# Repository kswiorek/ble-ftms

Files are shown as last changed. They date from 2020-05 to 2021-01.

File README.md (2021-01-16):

# Arduino BLE Indoor Bike Fitness Machine

This project uses two ESP32 boards to emulate an expensive indoor bike trainer and a power meter.<br/>
<br/>
One ESP measures power and cadence on a crank, the other receives these values, emulates a trainer and forwards the data. It also receives the simulation parameter from a computer and sets position of the resistance screw accordingly.<br/>
The data is also displayed on a 12864 screen and the user is able to change the resistance in ERG mode and the gears in simulation mode.<br/>
The user can also load a file with resistance values and times when to set them on an SD card.<br/>
The whole "realistic physics" part turned out to be more annoying to set up than realistic, so I added a configurator, with which the user can graphicaly define the function converting from the simulated grade to the resistance. More described in the instructable.
<br/><br/>
The promissed instructable <a href="https://www.instructables.com/DIY-Indoor-Bike-Smart-Trainer/?cb=1604870523">https://www.instructables.com/DIY-Indoor-Bike-Smart-Trainer/?cb=1604870523</a>

If you want to dig deaper into the code I highly suggest reading the "Fitness Machine Service" specifications
<a href="https://www.bluetooth.com/specifications/gatt/">https://www.bluetooth.com/specifications/gatt/</a>

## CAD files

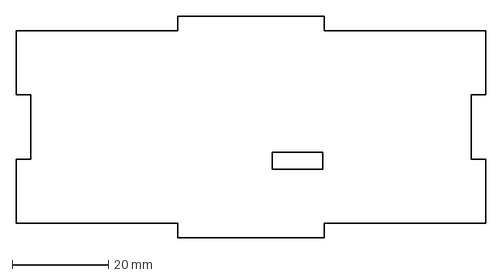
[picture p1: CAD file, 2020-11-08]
dxf/console/right.dxf
97.3 x 46.0 mm

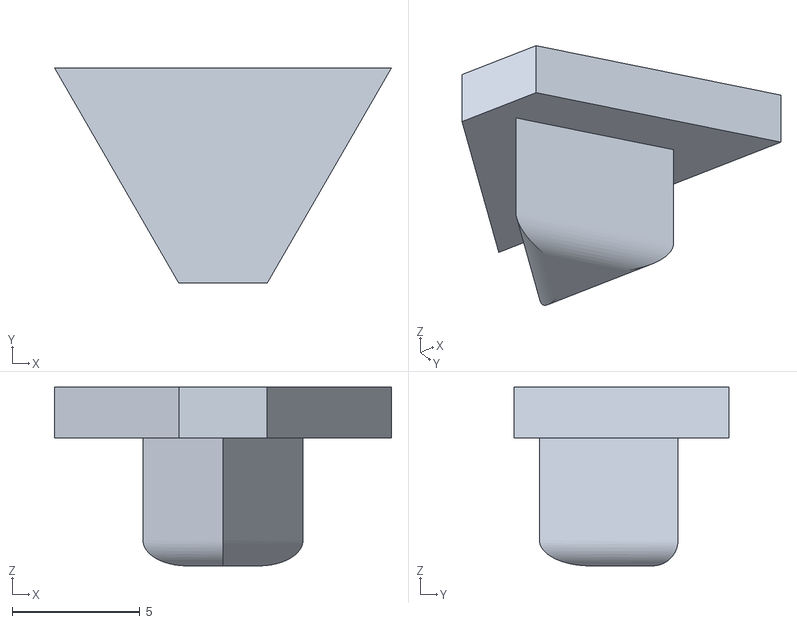
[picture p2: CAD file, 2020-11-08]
stl/bt1.stl
13.2 x 8.43 x 7.00

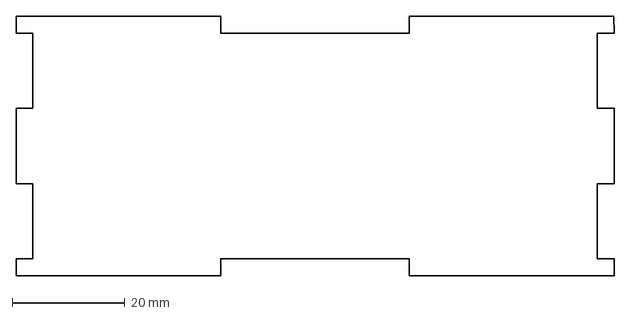
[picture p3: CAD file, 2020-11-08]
dxf/console/back.dxf
106.0 x 46.0 mm

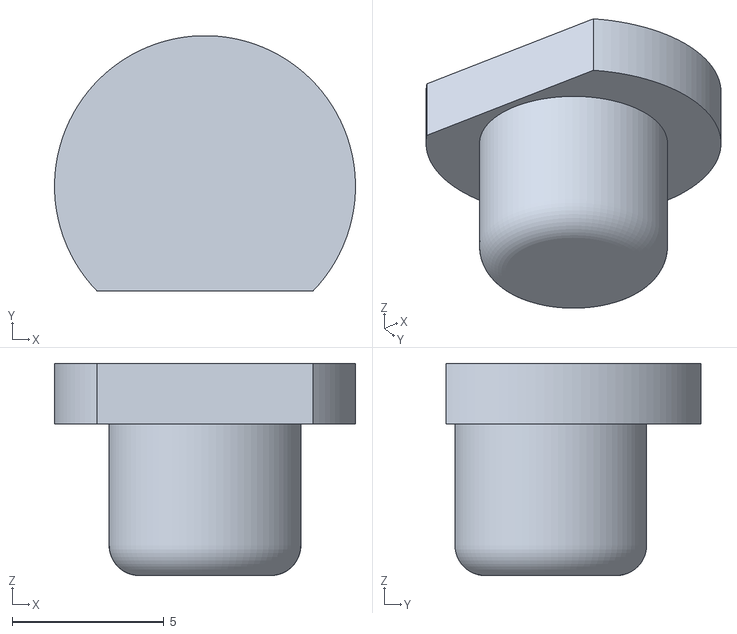
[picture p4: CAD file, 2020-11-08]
stl/bt3.stl
9.93 x 8.43 x 7.00

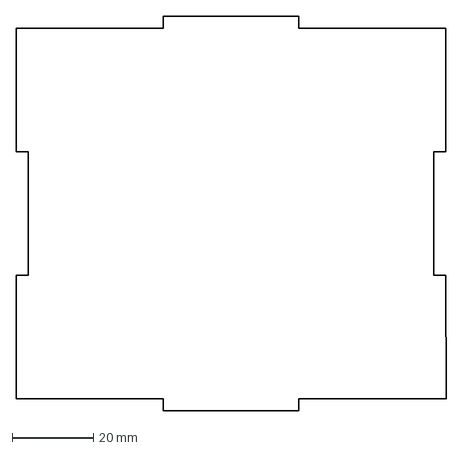
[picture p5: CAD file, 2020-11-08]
dxf/console/bottom.dxf
106.0 x 97.3 mm

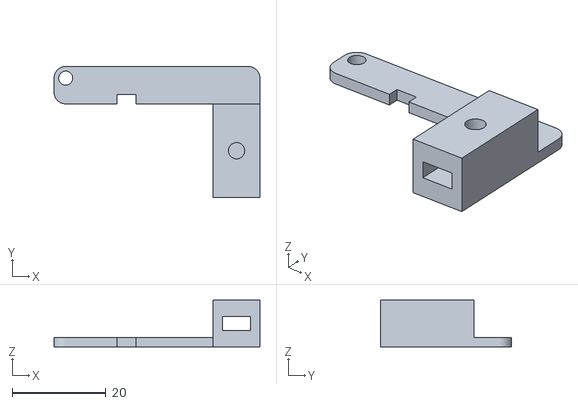
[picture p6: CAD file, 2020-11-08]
stl/pcb holder.stl
44.0 x 28.0 x 10.0

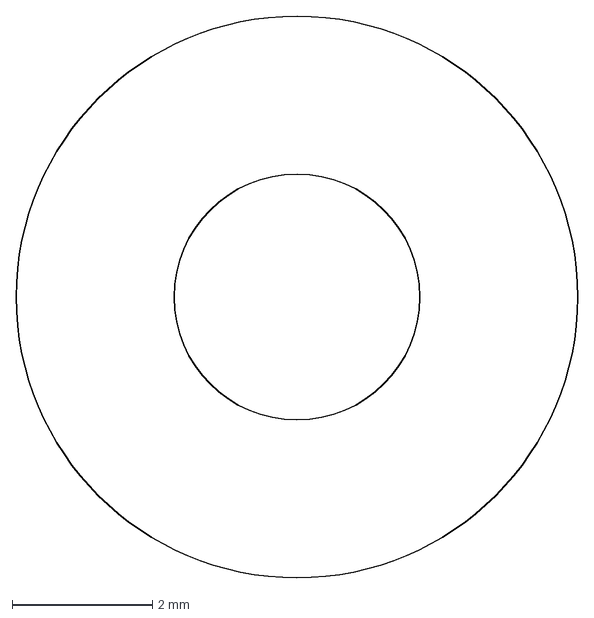
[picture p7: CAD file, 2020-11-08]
dxf/console/spacer.dxf
8.00 x 8.00 mm

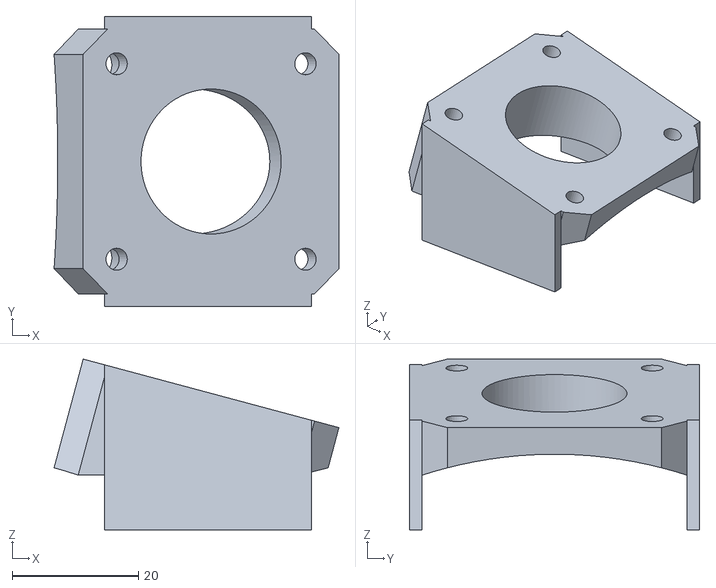
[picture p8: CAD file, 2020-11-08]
stl/motor mount.stl
45.2 x 46.0 x 27.1

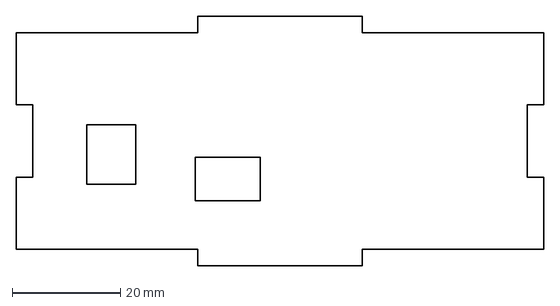
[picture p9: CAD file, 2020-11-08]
dxf/console/left.dxf
97.3 x 46.0 mm

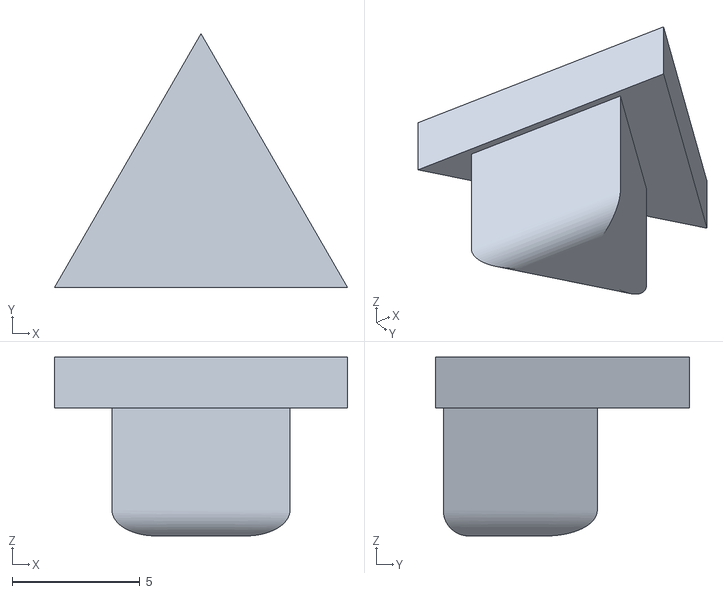
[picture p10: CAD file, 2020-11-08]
stl/bt2.stl
11.5 x 9.93 x 7.00

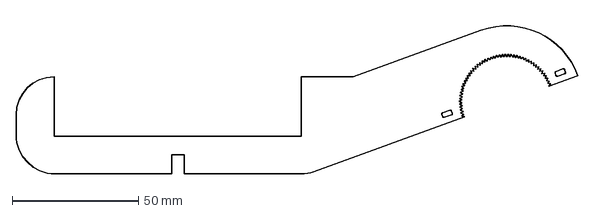
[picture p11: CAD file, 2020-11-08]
dxf/console/arm.dxf
222.8 x 62.6 mm

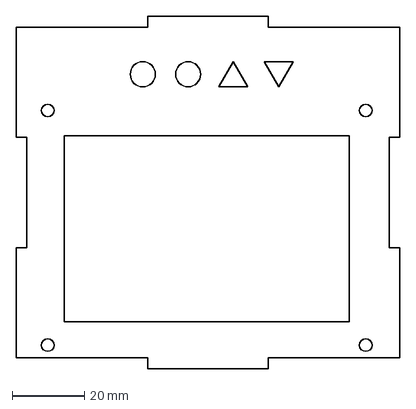
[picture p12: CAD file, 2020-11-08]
dxf/console/top.dxf
106.0 x 97.3 mm

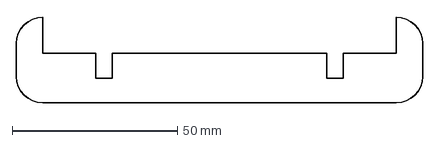
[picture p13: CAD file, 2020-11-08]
dxf/console/connector.dxf
123.0 x 26.0 mm

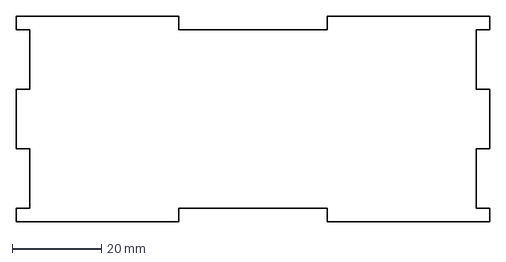
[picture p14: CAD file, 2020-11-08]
dxf/console/front.dxf
106.0 x 46.0 mm

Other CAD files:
fusion360/console.f3d
fusion360/motor mount.f3d
fusion360/pcb holder.f3d
fusion360/spacer.f3d

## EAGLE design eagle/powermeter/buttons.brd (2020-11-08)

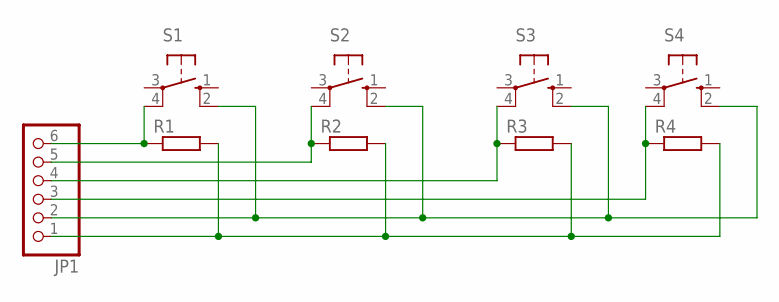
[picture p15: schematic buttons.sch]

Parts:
JP1: PINHD-1X6/90; 1X06/90
R1, R2, R3, R4: R-EU_0207/10; 0207/10
S1, S2, S3, S4: 10-XX; B3F-10XX

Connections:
unnamed: JP1.6, R1.1, S1.4 (P1)
unnamed: JP1.5, R2.1, S2.4 (P1)
unnamed: JP1.4, R3.1, S3.4 (P1)
unnamed: JP1.3, R4.1, S4.4 (P1)
unnamed: JP1.2, S1.2 (S1), S2.2 (S1), S3.2 (S1), S4.2 (S1)
unnamed: JP1.1, R1.2, R2.2, R3.2, R4.2

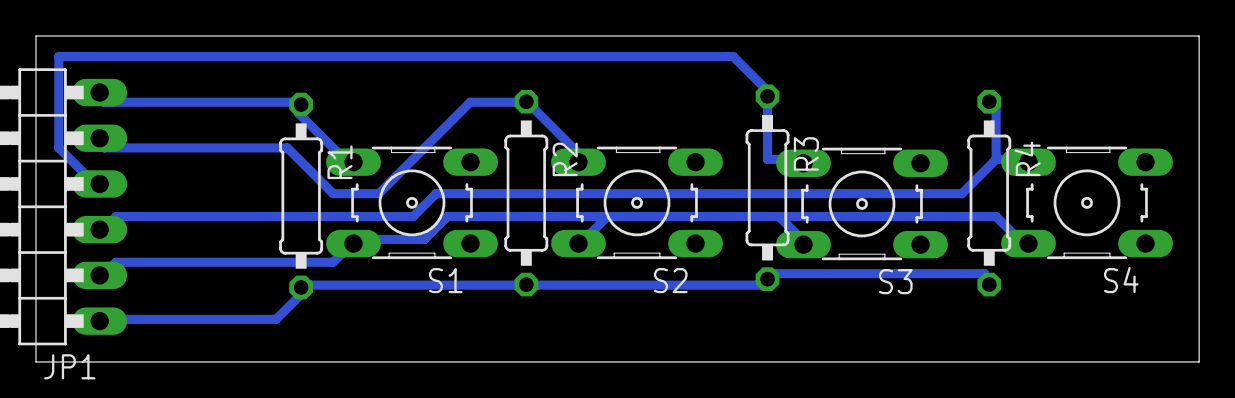
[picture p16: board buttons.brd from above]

Board: 2 copper layers, 64.6 x 18.1 mm, 9 parts (0 on the bottom side), 6 nets.

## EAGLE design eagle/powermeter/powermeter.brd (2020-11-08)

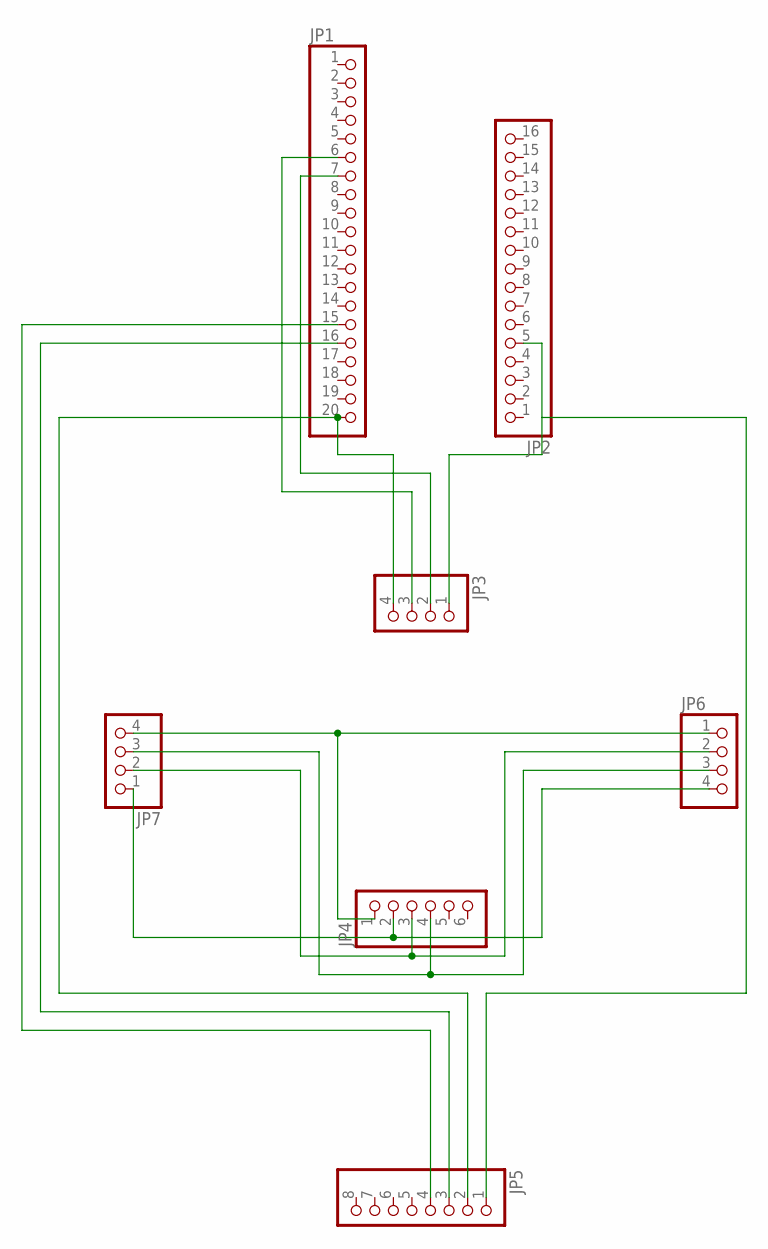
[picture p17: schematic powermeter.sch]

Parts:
JP1: PINHD-1X20; 1X20
JP2: PINHD-1X16; 1X16
JP3, JP6, JP7: PINHD-1X4; 1X04
JP4: PINHD-1X6; 1X06
JP5: PINHD-1X8; 1X08

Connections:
unnamed: JP4.1, JP6.1, JP7.4
unnamed: JP4.2, JP6.4, JP7.1
unnamed: JP4.3, JP6.2, JP7.2
unnamed: JP4.4, JP6.3, JP7.3
unnamed: JP1.20, JP3.4, JP5.2
unnamed: JP1.6, JP3.3
unnamed: JP1.7, JP3.2
unnamed: JP1.15, JP5.4
unnamed: JP2.5, JP3.1, JP5.1
unnamed: JP1.16, JP5.3

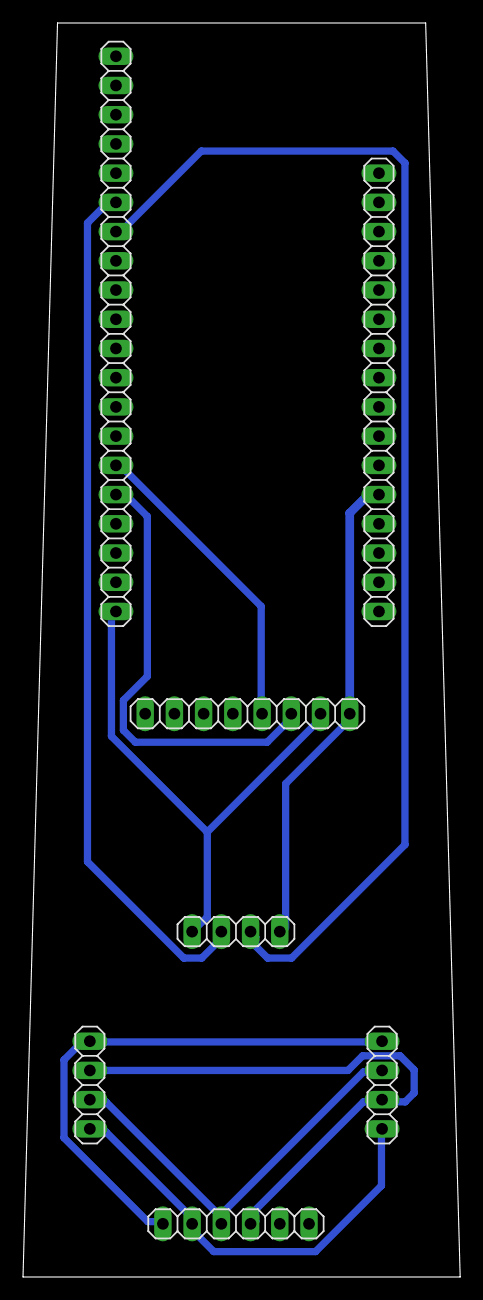
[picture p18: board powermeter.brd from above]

Board: 2 copper layers, 38.0 x 109.0 mm, 7 parts (0 on the bottom side), 10 nets.

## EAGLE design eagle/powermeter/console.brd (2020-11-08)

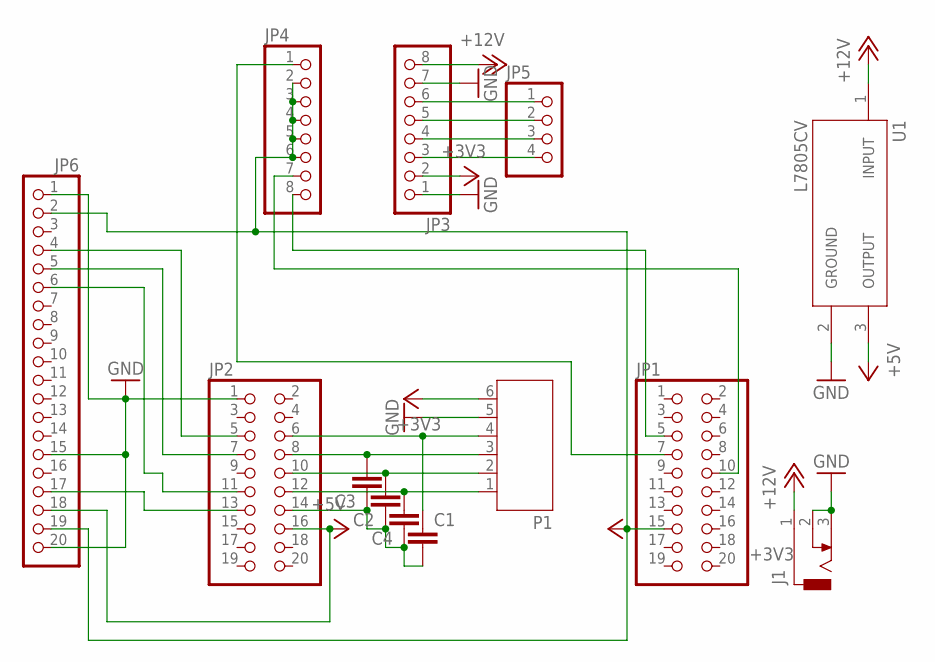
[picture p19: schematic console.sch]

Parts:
C1, C2, C3, C4: C-EU025-030X050; C025-030X050
J1: DCJ0303
JP1, JP2: PINHD-2X10; 2X10
JP3, JP4: PINHD-1X8; 1X08
JP5: PINHD-1X4/90; 1X04/90
JP6: PINHD-1X20; 1X20
P1: JST-PH6
U1: L7805CV; TO255P1040X460X1968-3

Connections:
+3V3: JP1.15, JP3.2, JP4.2, JP4.3, JP4.4, JP4.5, JP4.6, JP6.2, JP6.19, P1.6
+5V: JP2.16, JP6.18, U1.3 (OUTPUT)
+12V: J1.1, JP3.8, U1.1 (INPUT)
GND: J1.2, J1.3, JP2.1, JP3.1, JP3.7, JP6.1, JP6.15, JP6.20, P1.5, U1.2 (GROUND)
unnamed: C2.2, JP2.10, P1.2
unnamed: C3.2, JP2.8, P1.3
unnamed: C1.1, JP2.6, P1.4
unnamed: JP2.5, JP6.4
unnamed: JP2.13, JP6.17
unnamed: JP2.7, JP6.5
unnamed: C4.2, JP2.12, P1.1
unnamed: JP1.7, JP4.1
unnamed: JP3.6, JP5.1
unnamed: JP1.10, JP4.7
unnamed: JP1.5, JP4.8
unnamed: JP3.5, JP5.2
unnamed: JP3.4, JP5.3
unnamed: JP3.3, JP5.4
unnamed: C1.2, C2.1, C3.1, C4.1, JP2.14
unnamed: JP2.11, JP6.6

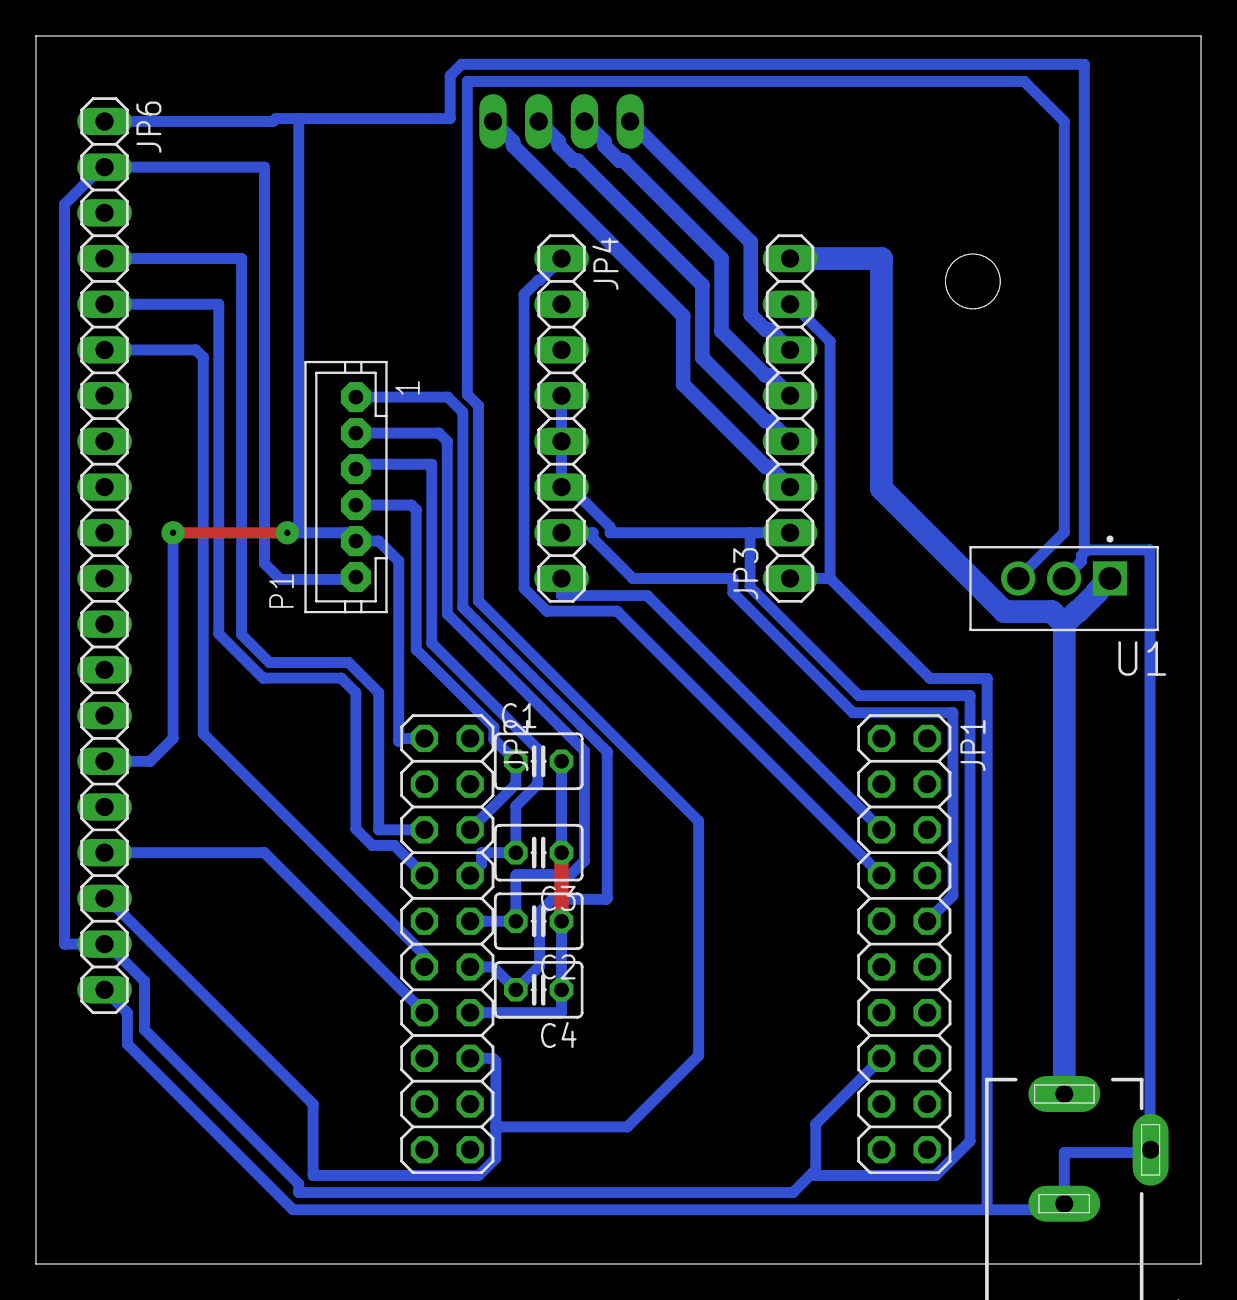
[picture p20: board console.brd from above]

Board: 2 copper layers, 64.8 x 68.2 mm, 13 parts (1 on the bottom side), 20 nets.

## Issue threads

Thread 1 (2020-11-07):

Instructables

paytufo, 2020-11-07:
Did you do the instructables guide finaly?

kswiorek, 2020-11-07:
I unfortunately didn't have the time, but I think you've motivated me enough to finally do this. I never actually suspected anyone would look at this.

paytufo, 2020-11-08:
Thank you! I'm starting to learn some code but I'm pretty noob. I've many time searching this solution to my dumb bike trainer.  My idea is to build an open bike trainer for people who like DIY. A BLDC trainer like Tacx NEO or Wahoo. Your code could be the first step to develop this trainer.

kswiorek, 2020-11-08:
I've made the instructable, I still need to upload some other files here, but the main thing is done [https://www.instructables.com/DIY-Indoor-Bike-Smart-Trainer/?cb=1604870523](url)

doudar, 2020-11-09:
Oh wow....I've skimmed across your repo before but now that you did the instructable. Now I know what its for. lol.........check this out:

https://github.com/doudar/SmartSpin2k-PlatformIO

I bet we could have saved each other a bunch of time. I've been wracking my head on that buggy ESP bluetooth library for a year in my spare time.

Maybe we should collaborate? :)

kswiorek, 2020-11-09:
Nice project! Far more professional than mine... It looks like you've got everything figured out. I will gladly help, but I'm not much of a coder - this whole thing is bodged together from some examples. I focused more on the physics of a realistic simulation. In theory this should be just as a normal bike - it even has the correct ratios of gears taken from a real road bike.
I also prefer to mount everything on one PCB - the wires often break and short, it always annoys me.

doudar, 2020-11-09:
I would *love* to see a carrier PCB if you thought it was possible. Possibly with an integrated dc-dc converter. I don't really have issues with wires breaking if they're done correctly but they do make assembly a pain.

Anyway, awesome project of yours too! I wouldn't have had any idea on where to start with that load cell stuff that you did.

Closed 2020-11-08.

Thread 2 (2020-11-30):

Thany you!

sife14, 2020-11-30:
I just want to say thank you for your amazing work. I have searched for implementation of the FTMS for ESP32 for hours until I found your amazing project. I really like the idea of the virtual gearing.

The only problem I experienced with your implementation, was an unstable connection to the virtual bike trainer software, which I fixed by adding a delay in the main loop. It seems like it was sending data to fast. I don't know if this issue also existed in the original code, since I modified your code quite a bit to fit to my hardware needs.

kswiorek, 2020-11-30:
I'm glad that I could help. I wanted to share this so I can save people some time, as I spent tens of hours without the help of any examples.
The delay might have helped - the graphical LCD I'm using takes quite a long time to write to, so the delay creates itself, but without it the loop may indeed run too quickly. I don't like using the "delay" function, because it stops any inputs and the refreshing of the LCD. I would use the something like this: `if millis()%100 { [send data] }` this would send the data every 100ms, but the LCD would still refresh as quickly as it can.

doudar, 2020-11-30:
I didn't look at the code, but vtaskdelay() should be your go to on the ESP32 as it lets other threads run. Regular delay() blocks anything else from running.

Closed 2020-12-04.

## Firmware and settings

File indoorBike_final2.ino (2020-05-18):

#include "BLE.h"
#include <SPI.h>
#include <U8g2lib.h>
#include <AccelStepper.h>
#include <EEPROM.h>
#include "soc/timer_group_struct.h"	
#include "soc/timer_group_reg.h"	// nesessary for avoiding watchdog triggering on the stepper core
#include "FS.h"
#include "SD.h"
#include "SPI.h"

#define wholeWeight 720			// weight of bicycle and rider
#define wheelDiameter 0.33
#define motorRpm 60				// RPM of the stepper motor

#define motorSteps 3200.0		// steps per revolution, needs to be float for calculations

const int levelSteps = 40;		// resistance steps 
#define rotations 4.5			// rotations of the screw for the steps

#define button1 25				// pin of pause button 
#define button2 32				// pin of enter button
#define button3 22				// pin of decrement button
#define button4 21				// pin of increment button

#define interruptTime 70		// miliseconds for debouncing buttons

const int lowCal[3] =	{ 60, 10, 30 }; // cadence[rpm], level, power[W]
const int highCal[3] =	{ 60, 20, 150 }; // cadence[rpm], level, power[W]

float lowTorque = lowCal[2] / ((lowCal[0] / 60.0) * 6.28);		// wheel torque on the low point of calibration
float highTorque = highCal[2] / ((highCal[0] / 60.0) * 6.28);	// wheel torque on the high point of calibration

int gearIndex;
#define gearNum 22			// number of gears
float gears[gearNum] = { 	// gear ratios
	0.323529412,
	0.382352941,
	0.441176471,
	0.458333333,
	0.5		   ,
	0.541666667,
	0.558823529,
	0.617647059,
	0.625	   ,
	0.705882353,		 
	0.708333333,
	0.791666667,
	0.823529412,
	0.875	   ,
	0.941176471,
	1		   ,
	1.088235294,
	1.166666667,
	1.235294118,
	1.333333333,
	1.541666667,
	1.75
};

// lcd defined
U8G2_ST7920_128X64_F_SW_SPI u8g2(U8G2_R0, /* clock=*/ 16 /* A4 */, /* data=*/ 17 /* A2 */, /* CS=*/ 0 /* A3 */, /* reset=*/ 4);
AccelStepper stepper = AccelStepper(1, 33, 26); // stepper defined

TaskHandle_t Task1;	// label for the stepper task

int16_t setPos, curPos;
int scroll;
float level;
bool zero;
bool psB;
bool enterB;
bool menu;

void IRAM_ATTR incr()	  // function to increment the level, gear index or scroll, with debouncing
{
	static unsigned long last_interrupt_time = 0;
	unsigned long interrupt_time = millis();
	if (interrupt_time - last_interrupt_time > interruptTime)
	{
		if (!menu) 
		{
			if (!sim)
			{
				level = int(level);
				level++;
			}
			else
			{
				gearIndex++;
				gearIndex = constrain(gearIndex, 0, gearNum-1);
			}
		}
		else scroll++;
	}
	last_interrupt_time = interrupt_time;
}
void IRAM_ATTR decr()	  // function to decrement the level, gear index or scroll, with debouncing
{
	static unsigned long last_interrupt_time = 0;
	unsigned long interrupt_time = millis();
	if (interrupt_time - last_interrupt_time > interruptTime)
	{
		if (!menu) 
		{
			if (!sim)
			{
				level = int(level);
				level--;
			}
			else
			{
				gearIndex--;
				gearIndex = constrain(gearIndex, 0, gearNum-1);
			}
		}
		else scroll--;
	}
	last_interrupt_time = interrupt_time;
}

void IRAM_ATTR enter()
{
	static unsigned long last_interrupt_time = 0;
	unsigned long interrupt_time = millis();
	if (interrupt_time - last_interrupt_time > interruptTime)
	{
		if (menu) enterB = true;
		menu = true;
		psB = true;
	}
	last_interrupt_time = interrupt_time;
}

void IRAM_ATTR ps()
{
	static unsigned long last_interrupt_time = 0;
	unsigned long interrupt_time = millis();
	if (interrupt_time - last_interrupt_time > interruptTime)
	{
		if (!menu) psB = !psB;
		menu = false;
	}
	last_interrupt_time = interrupt_time;
}

void setup() {
	Serial.begin(115200);
	BLEDevice::init("IndoorBike"); // name of the ble devicev
	while (!connectToServer());
	InitBLEServer();
	
	u8g2.begin();
	u8g2.clearBuffer();
	while (!SD.begin()) {    	   // while the card isnt initialized display message
		u8g2.setFont(u8g2_font_ncenB14_tr);
		u8g2.setCursor(33, 30);
		u8g2.print("WLOZ");
		u8g2.setCursor(28, 48);
		u8g2.print("KARTE");
		u8g2.sendBuffer(); 
		delay(200);   
	}

	xTaskCreatePinnedToCore(	   // setup the task for the second core
	                  Task1code,
		/* Task function. */
	                  "Task1",
		/* name of task. */
	                  10000,
		/* Stack size of task */
	                  NULL,
		/* parameter of the task */
	                  1,
		/* priority of the task */
	                  &Task1,
		/* Task handle to keep track of created task */
	                  0);          /* pin task to core 0 */
	
	stepper.setMaxSpeed(motorRpm / 60 * 3200);	// setup the motor																						 
	stepper.setSpeed(motorRpm / 60 * 3200);
	stepper.setAcceleration(12800);
	stepper.setEnablePin(27);					// enable pin
	stepper.setPinsInverted(0, 0, 1);

	pinMode(button1, INPUT);
	pinMode(button2, INPUT);
	pinMode(button3, INPUT);
	pinMode(button4, INPUT);	   	

	EEPROM.begin(4);
  
	level = EERead(2);
	Serial.println(level);
	curPos = EERead(0);
	Serial.println(curPos);
	stepper.setCurrentPosition(curPos);
	stepper.enableOutputs();
	menu = false;
	psB = true;
}
File file;
int values[64], valIndex;
long pauseStart, pauseEnd, pauseTot, playTime;
bool pauseTest, levelTest = true;
int zeroCnt, loopCnt;
void loop() {
	if (sim) // if in simulation mode (not ERG)
	{	
		float setTorque = (((grade / 10000.0)*wholeWeight) * wheelDiameter)+5.5;  // calculated set resistance torque on the wheel + torque on flat road
		Serial.println(setTorque);
		Serial.println(grade);
		float pedalTorque = gears[gearIndex]*setTorque;	 // set torque on the crank
		Serial.println(gears[gearIndex]);
		Serial.println(pedalTorque);
		level = mapF(pedalTorque, lowTorque, highTorque, lowCal[1], highCal[1]);	// mapped to the level settings
		Serial.println(level);
		level = constrain(level, 0, levelSteps);
		
																	
	}
	speedOut = (cadenceIn * 2.75 * 2.08 * 60*gears[gearIndex]) / 10;						// calculated speed, required by the specification
	indoorBikeDataCharacteristicData[2] = (uint8_t)(speedOut & 0xff);
	indoorBikeDataCharacteristicData[3] = (uint8_t)(speedOut >> 8);							// speed value with little endian order
	indoorBikeDataCharacteristicData[4] = (uint8_t)((cadenceIn * 2) & 0xff);				
	indoorBikeDataCharacteristicData[5] = (uint8_t)((cadenceIn * 2) >> 8);					// cadence value
	indoorBikeDataCharacteristicData[6] = (uint8_t)(constrain(powerIn, 0, 4000) & 0xff);
	indoorBikeDataCharacteristicData[7] = (uint8_t)(constrain(powerIn, 0, 4000) >> 8);		// power value, constrained to avoid negative values, although the specification allows for a sint16
    
	indoorBikeDataCharacteristic.setValue(indoorBikeDataCharacteristicData, 8);				// values sent
	indoorBikeDataCharacteristic.notify();	 												// device notified
	
	if (digitalRead(button2))zeroCnt++; // counter for button hold used for homing
	else zeroCnt = 0;
	if (!menu) { // if menu isn't on, display values
		u8g2.clearBuffer();
		u8g2.setFont(u8g2_font_ncenB14_tr);
		u8g2.setCursor(100, 32 + 7);
		if (!sim) u8g2.print(int(level));
		else	 u8g2.print(gearIndex);
		u8g2.setCursor(2, 30);
		u8g2.print(String(powerIn));
		u8g2.setCursor(2, 50);
		u8g2.print(String(cadenceIn));
		u8g2.setFont(u8g2_font_6x10_tf);
		u8g2.setCursor(1 + (12*String(powerIn).length()), 30);
		u8g2.print("W");
		u8g2.setCursor(1 + (12*String(cadenceIn).length()), 50);
		u8g2.print("rpm");
		u8g2.setFont(u8g2_font_6x13_tf);
		u8g2.setCursor(2, 11);			
		u8g2.print(file.name());
		if (psB && millis() % 2000 > 1000) // blinking "pause" sign
		{
			u8g2.setCursor(97, 11);
			u8g2.print("PAUZA");
		}
		u8g2.sendBuffer();
	}
	else
	{
		u8g2.clearBuffer();
		u8g2.drawRFrame(0, 0, 128, 64, 7);
		File root = SD.open("/");
		file = root.openNextFile();
		if (!file) {
			u8g2.setFont(u8g2_font_ncenB14_tr);
			u8g2.setCursor(30, 32 + 7);
			u8g2.print("Brak plikow");	 // no files
		}
		else  // display file list end show cursor
		{
			String files[32];
			int i = 0;
			u8g2.setFont(u8g2_font_6x13_tf);
			while (file) {        
				if (!(bool)file.isDirectory())
				{
					files[i] = file.name();
					i++;
				}
				file = root.openNextFile();
			}
			for (i = 0; i < 5; i++)
			{
				int scrollPrev;
				if (files[int(i + 5*(floor(scroll / 5)))] != "")
				{
					u8g2.setCursor(20, 14 + (i * 11));
					u8g2.print(files[int(i + 5*(floor(scroll / 5)))]);
				}      
			}
			if (files[scroll] == "") scroll = scroll - 1;
			u8g2.setCursor(5, 14 + ((scroll % 5) * 11));
			u8g2.print("->");

			if (enterB)  // chose file and close the menu
			{
				file = SD.open(files[scroll]);
				Serial.println(file.name());
				enterB = false;
				menu = false;
				String content = file.readString();	   //read file contents
				Serial.println(content);

				int lastIndex = 0;
				int index = content.indexOf(";", lastIndex);
				i = 0;
				while (index >= 0) // get the list of settings
				{
					values[i] = content.substring(lastIndex, index).toInt();
					lastIndex = index + 1;
					index = content.indexOf(";", lastIndex);
					i++;
				}
				psB = true;
				pauseTot = pauseTot + playTime;
				valIndex = 0;
			}
		}
		u8g2.sendBuffer();
	}

	if (psB&&pauseTest)			// deal with pausing
	{
		pauseStart = millis();
		pauseTest = false;
	}
	else if (!psB && !pauseTest)
	{
		pauseEnd = millis();
		pauseTest = true;
		pauseTot = pauseTot + (pauseEnd - pauseStart);
	}

	if (!psB)
	{
		playTime = millis() - pauseTot;
		Serial.println(playTime);
		if (values[valIndex] == playTime / 1000 && levelTest)
		{
			levelTest = false;
			level = values[valIndex + 1];
			valIndex = valIndex + 2;
		}
		else if (values[valIndex] != playTime / 1000) levelTest = true;
	}
  
	if (level > levelSteps) level = levelSteps;
	if (level < 0) level = 0;
	if (scroll < 0) scroll = 0;
	setPos = mapF(level, 0.0, levelSteps, 0.0, motorSteps*rotations);
	Serial.print("setPos	");
	Serial.println(setPos);
	if ((curPos != setPos && !zero) && level >= 0 && level <= levelSteps) // move the motor to a new position
	{
    
		stepper.moveTo(setPos);
		curPos = setPos;

		EEWrite(curPos, 0);
		EEWrite(level, 2);
    
		Serial.println(curPos);
		Serial.println(level);
	}
	if (zeroCnt > 30) zero = true;
	Serial.println(zeroCnt);
	if (zero)		 // move to the end of travel until motor loses steps
	{
		Serial.println("Homing");
		curPos = 0;   
		EEWrite(curPos, 0);
		u8g2.clearBuffer();
		u8g2.setFont(u8g2_font_ncenB14_tr);
		u8g2.setCursor(3, 32 + 7);
		u8g2.print("ZEROWANIE");
		u8g2.sendBuffer();
		stepper.setMaxSpeed(300 / 60 * 3200);
		stepper.moveTo(-(int(rotations*motorSteps)));
		//Serial.println(-(rotations*motorSteps));
		delay(5000);
		curPos = 0;  
		level = 0; 
		stepper.setCurrentPosition(0); 
		stepper.setMaxSpeed(motorRpm / 60 * 3200);
		zero = false;
		menu = false;
	}
	//stepper.run();
}

void EEWrite(int16_t inp, int reg) //write a word to eeprom on register
{
	word ee;
	//Serial.println(inp);
	ee = inp & 0xFF00;
	ee = ee >> 8;
	EEPROM.write(reg, ee);
	ee = inp & 0xFF;
	EEPROM.write(reg + 1, ee);
	EEPROM.commit();
}

int16_t EERead(int reg)			   // read a word on register
{
	word ee;
	ee = EEPROM.read(reg);
	ee = ee << 8;
	ee = ee + EEPROM.read(reg + 1);
	return ee;
}
bool test;
void Task1code(void * parameter) {	   // handle the stepper and button on the other core. Interrupts break bluetooth
	for (;;) {
		TIMERG0.wdt_wprotect = TIMG_WDT_WKEY_VALUE;	   // the loop needs to run fast, this disables the watchdog
		TIMERG0.wdt_feed = 1;
		TIMERG0.wdt_wprotect = 0;

		if (stepper.isRunning()) stepper.enableOutputs();
		else                    stepper.disableOutputs();
    
		stepper.run();
		if (digitalRead(button4)) incr();
		if (digitalRead(button3)) decr();
		if (digitalRead(button2)) enter();
		if (digitalRead(button1)) ps();
		delayMicroseconds(10);
	}
}

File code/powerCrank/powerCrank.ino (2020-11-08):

#include "HX711.h"
#include <Adafruit_MPU6050.h>

#include <Wire.h>
#include <math.h>
#include <EEPROM.h>

// all must be floats for calculations
#define sensMin -200941.0  // reading of the sensor with 0 force
#define sensMax -351117.0  // reading of the sensor with weightMax of force
#define weightMax 120.0
#define radius 0.175		   // distance form crank center to pedal center
#define sensRadius 0.115   // distance of the MPU sensor to crank center 

#define zeroAngle 180	   // angle, where to tare - all angles according to the Cycling Power Measurement specifications
						   // left crank forward - 0 degrees
#define freq 0.5		   // notify frequency

#define LOADCELL_DOUT_PIN 16
#define LOADCELL_SCK_PIN 17

Adafruit_MPU6050 mpu;
HX711 scale;

#include <BLEDevice.h>
#include <BLEUtils.h>
#include <BLEServer.h>
#include <BLE2902.h>

#define SERVICE_UUID        "4fafc201-1fb5-459e-8fcc-c5c9c331914b"			// UUID of the service, random, must match the one on the console
#define POWER_CHARACTERISTIC_UUID "beb5483e-36e1-4688-b7f5-ea07361b26a8"	// UUID of the characteristic, random, must match the one on the console
#define CADENCE_CHARACTERISTIC_UUID "ceb5483e-36e1-4688-b7f5-ea07361b26a8"	// UUID of the characteristic, random, must match the one on the console

BLECharacteristic sendPower(POWER_CHARACTERISTIC_UUID, BLECharacteristic::PROPERTY_NOTIFY);
BLECharacteristic sendCadence(CADENCE_CHARACTERISTIC_UUID, BLECharacteristic::PROPERTY_NOTIFY);

// average variables:
// avr - rolling average lasts one rotation or 2 seconds
// avgFin - the final average of avr with the frequency of "freq"
long reading;
float weight, weightOld, power, rpm, avr;
double angle;
float reg[160];	// samples for the rolling average
bool test;

bool tareTest = true;
int samples, cnt, tareCnt, offCnt;
int8_t tare;
long avgFin;

bool _BLEClientConnected = false;

class MyServerCallbacks : public BLEServerCallbacks {
  void onConnect(BLEServer* pServer) {
    _BLEClientConnected = true;
    Serial.println("conn");
  };

  void onDisconnect(BLEServer* pServer) {
    _BLEClientConnected = false;
    Serial.println("disc");
  }
};

void InitBLE() {
    BLEDevice::init("crank");
    BLEServer *pServer = BLEDevice::createServer();
    pServer->setCallbacks(new MyServerCallbacks());
    
	BLEService *pPower = pServer->createService(SERVICE_UUID);

	pPower->addCharacteristic(&sendPower);
	BLE2902* powerDesc = new BLE2902();
	powerDesc->setIndications(1);                                       
	sendPower.addDescriptor(powerDesc);
	pPower->addCharacteristic(&sendCadence);
	BLE2902* cadenceDesc = new BLE2902();
	cadenceDesc->setIndications(1);
	sendCadence.addDescriptor(cadenceDesc);
	pServer->getAdvertising()->addServiceUUID(SERVICE_UUID);
	pServer->getAdvertising()->start();
	pPower->start();
}
  void onDisconnect(BLEServer* pServer) {
    _BLEClientConnected = false;
  }

void setup() {
    pinMode(32, OUTPUT);
    digitalWrite(32, HIGH);
    Serial.begin(115200);
    Serial.println("Start");
    InitBLE();
    mpu.begin();
    scale.begin(LOADCELL_DOUT_PIN, LOADCELL_SCK_PIN);
	
    mpu.setGyroRange(MPU6050_RANGE_2000_DEG);
    mpu.setFilterBandwidth(MPU6050_BAND_94_HZ);
    mpu.setAccelerometerRange(MPU6050_RANGE_8_G);
	// the mpu must be fast, therefore max setting
	
	pinMode(5, OUTPUT);	  // tare LED setup
	digitalWrite(5, HIGH);
	EEPROM.begin(1);		//read tare
	tare = EEPROM.read(0); 
}
uint8_t blink;
void loop() {
	cnt++;
  
    sensors_event_t a, g, temp;
    mpu.getEvent(&a, &g, &temp);
  
    reading = scale.read(); // sensor must be set in 80 Hz mode, otherwise the loop will run too slow
							// this blocking command provides timing
    weight = ((reading - sensMin) * (weightMax) / (sensMax - sensMin)); // calculate the force on the pedal in N

	// angle measurement from gravitaional acceleration
	// centripetal acceleration acceleration is accaunted for
	// the angle is adjusted to match the gatt specifications with fmod
    angle = fmod(((atan2(a.acceleration.y + (g.gyro.z*g.gyro.z*sensRadius), a.acceleration.x)) * 360 / 6.28) + 180, 360.0);  
	
	// if crank is in position and weight isn't changing increment counter
	// after slightly more than two seconds tare and write to eeprom 
	if ((abs(angle - zeroAngle) < 10) && (int(rpm) == 0) && tareTest && (abs(weight-weightOld)< 2)) 
	{       
		tareCnt++;
		digitalWrite(5, (blink & 0x8)); // blink LED if in position
		blink++;
		if (tareCnt >= 200)
		{
			tare = weight;
			EEPROM.write(0, tare);
			EEPROM.commit();
			digitalWrite(5, LOW);
			delay(1000);
			digitalWrite(5, HIGH);
			tareCnt = 0;
			
			tareTest = false;
			
		}
	}
	else if(!(abs(angle - zeroAngle) < 10 && int(rpm) == 0)) 
	{
		weightOld = weight;
		tareCnt = 0;
		//tareTest = 1;
		//Serial.println((int)tareTest);
		digitalWrite(5, HIGH);
	}
	
	
	weight -= tare;	// subtract tare
    power = (-g.gyro.z*radius*weight);  // calculate power from angular velocity and force, negative because of the sensor mounting

    reg[0] = power;	// 0th index assigned for rolling average 

    samples = constrain(abs(4800/rpm), 1, 160);	// calculate the number of samples taken into account
	
    for (int i=0; i<samples; i++)	// get the average
    {
    avr = avr + reg[i];
    }	
    avr = avr/samples;
	
    for (int i=160-2; i>=0; i--)	// shift the array
    {
    reg[i+1] = reg[i];
    }
  
    rpm = -(g.gyro.z/6.28)*60;		// calculate RPM from rotational velocity

    avgFin=avgFin+int(avr);			// sum the final average
  
    if(cnt>=(int(80/freq)))			// every 1/freq, 80 is the number of samples (loop repeats) per second
    {
      if (!_BLEClientConnected) offCnt++;
      else offCnt = 0;
    
      if (offCnt > 60*freq) esp_deep_sleep_start();
      avgFin = constrain((2*avgFin)/cnt, 0, 2000); // calculate the average - 2* for two legs (measuring only one)

	    int16_t power = (int16_t)avgFin;
	    int16_t cadence = (int16_t)rpm;
	    
	    uint8_t powerOut[2] = { (uint8_t)(power >> 8), (uint8_t)(power & 0xff) };		// set values
	    uint8_t cadenceOut[2] = { (uint8_t)(cadence >> 8), (uint8_t)(cadence & 0xff) };
	    
	    // send and notify
	    sendPower.setValue(powerOut, 2);
	    sendPower.notify();
	    sendCadence.setValue(cadenceOut, 2);
	    sendCadence.notify();
     Serial.println(offCnt);

	    // print data for debugging
        Serial.print("Kąt: ");
        Serial.print(angle);
        Serial.print("   ");

        Serial.print("Sila: ");
        Serial.print(weight);
        Serial.print("   ");
	    
	    Serial.print("Wartosc: ");
	    Serial.print(reading);
	    Serial.print("   ");

        Serial.print(" Tara: ");
        Serial.print(tare);
        Serial.print("   ");

  
        Serial.print(" S. moc: ");
        Serial.print(avgFin);
        Serial.print("   ");

        Serial.print(" Kadencja: ");
        Serial.print(rpm);
        Serial.print("   ");
  
  
        Serial.println();
        cnt = 0;
        avgFin = 0;
    }



}

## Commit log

2020-11-08 Add files via upload
    Added the Autodesk EAGLE project
    [buttons.brd, buttons.sch, console.brd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]
2020-11-08 Add files via upload
    Remaining project files
    [arm.dxf, back.dxf, bottom.dxf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]
2022-07-20 Added advertising flags
    3 days of debugging why RGT doesn't connect, one line added :)
    When the device sees those two flags it works for some reason, while iPhones do not care.
    [BLE.h]
